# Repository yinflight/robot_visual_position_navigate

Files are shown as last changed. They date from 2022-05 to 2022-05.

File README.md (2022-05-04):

# robot_visual_position_navigate
### 爆改车间主任的NN机器人项目
ESP8285为核心搭建振动运动微型机器人，python+openCV视觉控制规划机器人路径控制机器人轨迹运动。

模仿kilobot的运动结构制作的了这个微型的振动机器人，靠两个振动电机来控制机器人的前进和转向。

ESP-01F为模块主控，两个MOS管驱动振动电机，电路非常简单，电池使用了两粒电容形状的锂电池，主板上即成了串口转USB和充电电路。

单片机使用Arduino IDE 环境开发 附件中：NN-Robot_V1.0.ino

上位机Python3 + openCV开发 附件中: NN机器人路径规划.py

3D打印盖子 附件中：NN机器人盖子.STL

需要外设：USB摄像头

电池链接：https://item.taobao.com/item.htm?spm=a1z09.2.0.0.68572e8dqsq1kj&id=592452546258&_u=t2oqo1kf9c6b

开关链接：https://item.taobao.com/item.htm?spm=a1z09.2.0.0.68572e8dqsq1kj&id=569513203579&_u=t2oqo1kf3a2e

按钮链接：https://item.taobao.com/item.htm?spm=a1z09.2.0.0.68572e8dqsq1kj&id=12245619223&_u=t2oqo1kf7bd4

震动电机链接： https://detail.tmall.com/item.htm?id=635278031707&spm=a1z09.2.0.0.20e02e8dZ8Xvv3&_u=t2oqo1kf2414

探针链接： https://item.taobao.com/item.htm?spm=a1z09.2.0.0.20e02e8dZ8Xvv3&id=597188992248&_u=t2oqo1kf83ba （P50-T2/90度三面锥型头）

WS2812 2020灯珠链接 :https://item.taobao.com/item.htm?spm=a1z09.2.0.0.65002e8dNjQBp4&id=635162819740&_u=t2oqo1kf7104

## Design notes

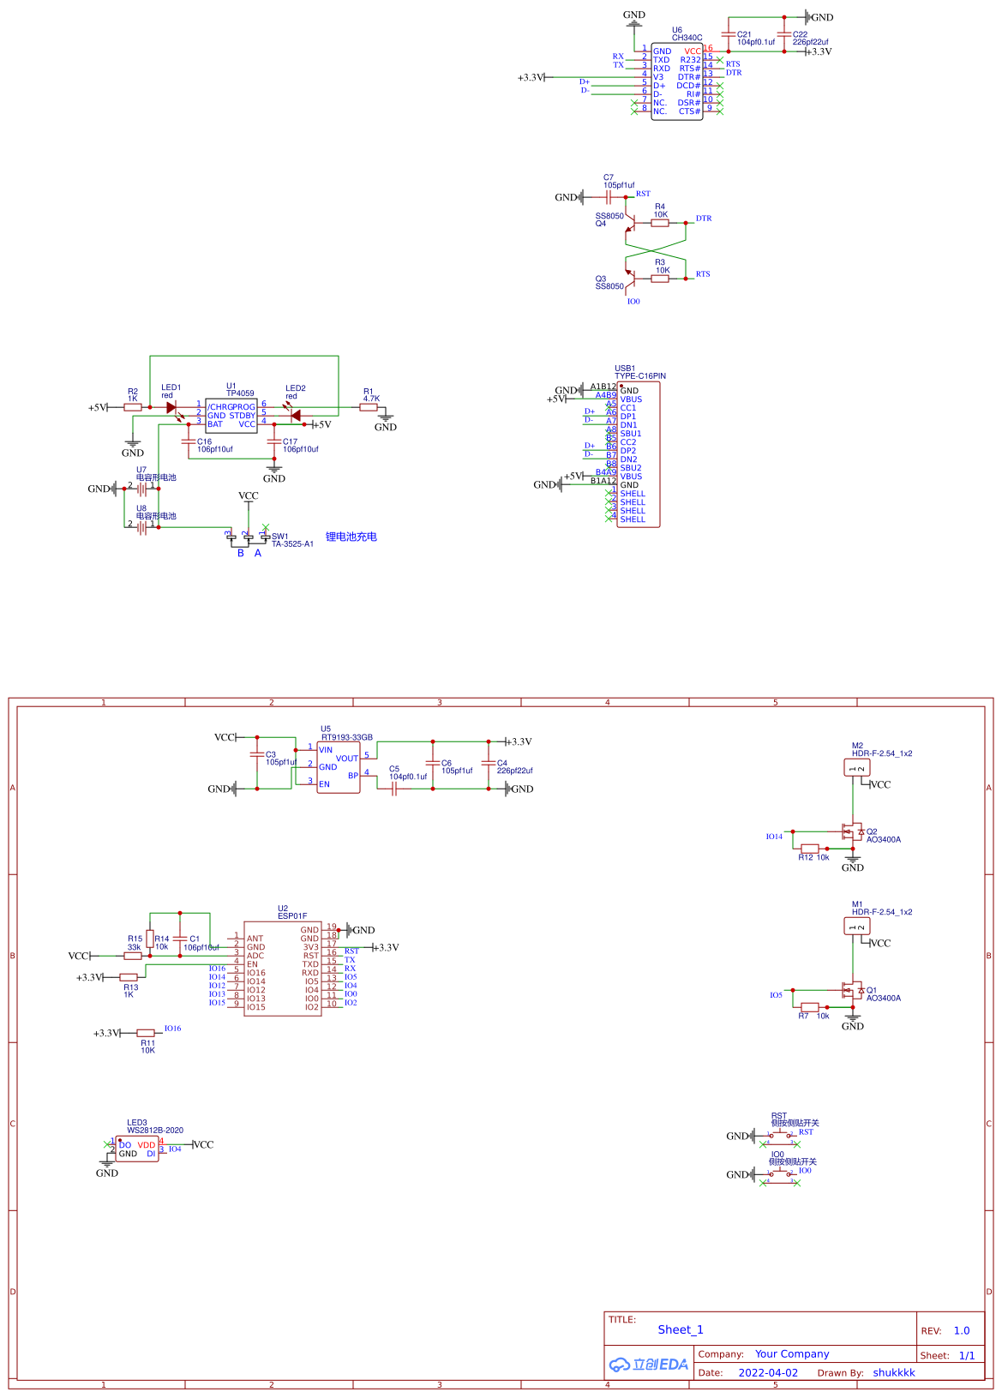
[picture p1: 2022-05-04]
f16584f0c2634fa2b6937635966befd9 (1).png

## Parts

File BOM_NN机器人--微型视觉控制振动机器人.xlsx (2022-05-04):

ID | Name | Designator | Footprint | Quantity
1 | 106pf10uf | C1,C16,C17 | C0603 | 3
2 | 105pf1uf | C3,C6,C7 | C0603 | 3
3 | 226pf22uf | C4,C22 | C0603 | 2
4 | 104pf0.1uf | C5,C21 | C0603 | 2
5 | 侧按侧贴开关 | IO0,RST | KEY-SMD_1TS003B | 2
6 | red | LED1,LED2 | LED0603-RD | 2
7 | WS2812B-2020 | LED3 | LED-SMD_4P-L2.0-W2.0-TL_WS2812B-2020 | 1
8 | HDR-F-2.54_1x2 | M1,M2 | HDR-F-2.54_1X2 | 2
9 | AO3400A | Q1,Q2 | SOT-23-3_L2.9-W1.6-P1.90-LS2.8-BR | 2
10 | SS8050 | Q3,Q4 | SOT-23-3_L2.9-W1.3-P1.90-LS2.4-BR | 2
11 | 4.7K | R1 | R0603 | 1
12 | 1K | R2,R13 | R0603 | 2
13 | 10K | R3,R4,R7,R12,R11,R14 | R0603 | 6
14 | 33K | R15 | R0603 | 1
15 | TA-3525-A1 | SW1 | SW-SMD_3P-L9.1-W3.5-P2.50-EH6.8 | 1
16 | TP4059 | U1 | SOT-23-6_L2.9-W1.6-P0.95-LS2.8-BR | 1
17 | ESP01F | U2 | ESP-01F | 1
18 | RT9193-33GB | U5 | SOT-23-5_L3.0-W1.7-P0.95-LS2.8-BR | 1
19 | CH340C | U6 | SOP-16_L10.0-W3.9-P1.27-LS6.0-BL | 1
20 | 电容形电池 | U7,U8 | 电容形电池 | 2
21 | TYPE-C16PIN | USB1 | USB-SMD_TYPE-C16PIN-1焊盘加长 | 1

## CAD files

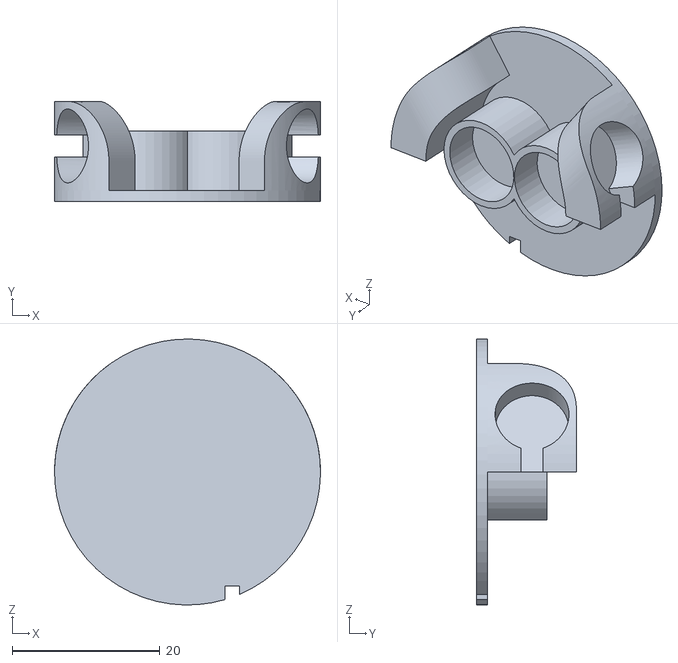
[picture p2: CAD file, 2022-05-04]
NN机器人盖子.STL
36.0 x 13.5 x 36.0

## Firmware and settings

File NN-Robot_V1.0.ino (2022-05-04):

//抖音爆改车间主任开源代码
//NN机器人单片机源码
//开发板选择ESP8285
//需要项目-加载库-库管理 中搜索安装FastLED库
//ESP8266 SDK版本为3.0.2
//烧录前先修改Wifi链接信息
//烧录结束后串口监视器查看并记录IP地址
//IO0按键切换 状态灯说明：红色闪烁=wifi链接中，蓝色常亮=视觉控制自动运动，绿色常亮=手动遥控
//转载保留爆改车间主任署名
//关注“爆改车间”微信公众号获取主任更多开关代码
//关注“爆改车间主任”抖音观看主任最新有趣视频

#include <ESP8266WiFi.h>
#include <WiFiUdp.h>
#include <FastLED.h>
#define NUM_LEDS 1  
#define DATA_PIN 4
CRGB leds[NUM_LEDS];

unsigned int localPort = 1234;      // 可以自定义端口号
WiFiUDP Udp;
char packetBuffer[UDP_TX_PACKET_MAX_SIZE + 1]; //buffer to hold incoming packet,

#ifndef STASSID
#define STASSID "******"    
#define STAPSK  "******"
#endif
const char* ssid     = STASSID;
const char* password = STAPSK;

const int M1 = 5;
const int M2 = 14;

const int LED =  4;
int BUT = 0;

int power = 256;
int dis,ste,ang,dir;
bool cont;
bool flash;

void LED_red_flash(){
  if(flash){
    leds[0] = CRGB::Red;
    FastLED.show();
    FastLED.show();
  }else{
    leds[0] = CRGB::Black;
    FastLED.show();
    FastLED.show();
  }
  flash = !flash;
}


void setup() {
  Serial.begin(115200);
  FastLED.addLeds<WS2811, DATA_PIN, GRB>(leds, NUM_LEDS);
  FastLED.setBrightness(50);
  Serial.println();
  Serial.println();
  Serial.println();
  pinMode(M1, OUTPUT);
  pinMode(M2, OUTPUT);
  pinMode(BUT, INPUT);
  
  digitalWrite(M1, LOW);
  digitalWrite(M2, LOW);
  
  // We start by connecting to a WiFi network

  Serial.println();
  Serial.println();
  Serial.print("Connecting to ");
  Serial.println(ssid);

  WiFi.mode(WIFI_STA);
  WiFi.begin(ssid, password);

  while (WiFi.status() != WL_CONNECTED) {
    delay(500);
    Serial.print(".");
    LED_red_flash();
  }

  Serial.println("");
  Serial.println("WiFi connected");
  digitalWrite(LED, HIGH);
  Serial.println("IP address: ");
  Serial.println(WiFi.localIP());
  leds[0] = CRGB::Blue;
  FastLED.show();
  FastLED.show();
  FastLED.show();
  
  Udp.begin(localPort);

}


String templine ="";
void loop() {
  int packetSize = Udp.parsePacket();
  
  if (packetSize) {

    int n = Udp.read(packetBuffer, UDP_TX_PACKET_MAX_SIZE);
    packetBuffer[n] = 0;
    Serial.print("收到数据:");
    Serial.println(packetBuffer);
    Serial.print("发送端IP：");
    Serial.print(Udp.remoteIP().toString().c_str());
    Serial.println(Udp.remotePort());

    String line = packetBuffer;
    String a = packetBuffer;

    if(line.indexOf("M1") != -1){  //左               //接收通道A处理
      turnL();
    }

    if(line.indexOf("M2") != -1){
      turnR();
    }

    if(line.indexOf("MM") != -1){
      forward();
    }
    if(line.indexOf("STOP") != -1){
      stop();
    }

    if(line.indexOf("W") != -1){
      templine=line.substring(line.indexOf("W"));
      power=templine.substring(1,templine.indexOf(",")).toInt();
      Serial.print("power: ");
      Serial.println(power);
    }
    
    if(line.indexOf("C") != -1){
      templine=line.substring(line.indexOf("C"));
      dis=templine.substring(1,templine.indexOf(",")).toInt();
      Serial.print("距离: ");
      Serial.println(dis);
    }

    if(line.indexOf("R") != -1){
      templine=line.substring(line.indexOf("R"));
      ang=templine.substring(1,templine.indexOf(",")).toInt();
      Serial.print("角度: ");
      Serial.println(ang);
    }

    if(line.indexOf("F") != -1){
      templine=line.substring(line.indexOf("F"));
      dir=templine.substring(1,templine.indexOf(",")).toInt();
      Serial.print("方向: ");
      Serial.println(dir);
    }
    
    if(cont == 0){
      if(dis > 25){
        if(ang>160){
          ste = 1;
        }else if( ang<20 and dis <80){
          ste = 1;  
        }else{
          if(dir <0){
            ste = 2;
          }else{
            ste = 3;
          }
        }
      }else{
        ste = 0;
      }

      switch(ste){
        case 0:
          stop();
          break;
        case 1:
          forward();
          break;
        case 2:
          turnR();
          break;
        case 3:
          turnL();
          break;
      }
    }
    
  }


  if(cont){
    leds[0] = CRGB(0,255,0);
    
    FastLED.show();
    FastLED.show();

  }else{
    leds[0] = CRGB(0,0,255);
    FastLED.show();
    FastLED.show();
  }
      
  if(digitalRead(BUT)==LOW){
    delay(20);
    if(digitalRead(BUT)==LOW){
      cont = !cont;
      while(digitalRead(BUT)==LOW);
    }
  }
}

void turnL(){
  analogWrite(M1, power);
  analogWrite(M2, 0);

}

void turnR(){
  analogWrite(M1, 0);
  analogWrite(M2, power);

}

void forward(){
  analogWrite(M1, power);
  analogWrite(M2, power);
}

void stop(){
  analogWrite(M1, 0);
  analogWrite(M2, 0);

}
